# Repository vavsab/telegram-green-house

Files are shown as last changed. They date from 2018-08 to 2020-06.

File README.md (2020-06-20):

# telegram-green-house 
[English version](README.EN.md)

Build Status (https://copter-monitor.visualstudio.com/copter-monitor/_build/latest?definitionId=1&branchName=master)

Открытый телеграм бот, который устанавливается в теплицу. 

## Основные функции:

* Отображение температуры и влажности
* Оповещение при превышениях температуры
* Отображение прогноза из сайта погоды (какого именно, задается в конфигурационном файле)
* Отображение графика температуры за последние сутки
* Запись коротких (до 1 мин) видео и фото из веб-камеры в теплице
* Ручное управление поливом. Управление по отрезкам времени дорабатывается.

# Демо

* [Телеграм-бот](https://t.me/demo_green_house_bot)
* [Эмулятор теплицы](http://demo.green.octopan.net:8081/) - позволяет выставить температуру/влажность и посмотреть, как на нее реагирует бот. Также здесь можно увидеть, включен или выключен свет и полив.
* [Веб-панель](http://demo.green.octopan.net:8080/) - урезанная версия бота. На данный момент только отображает температуру/влажность.

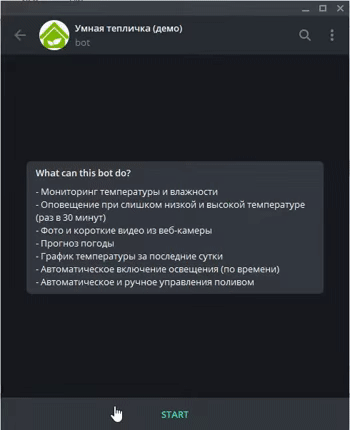
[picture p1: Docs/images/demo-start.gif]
Демо анимация


## Нюансы работы демо

* Отключена проверка прав доступа. В обычной версии нужно добавлять пользователей в конфигурационный файл, чтобы разрешить использование бота.
* Всегда отсылаются примеры фото и видео, т.к. в демо нет настоящей камеры.
* Доступен пример видео только для 5 секунд.

# Применение

Бот предназначен для установки в теплицу, которая находится в непосредственной близости от дома.

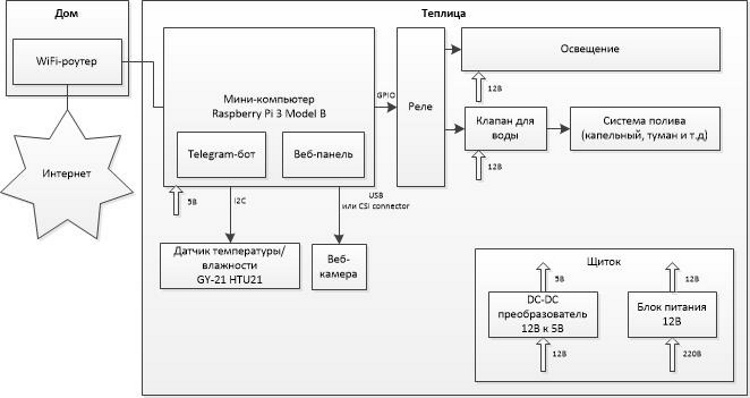
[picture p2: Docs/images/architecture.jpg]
Типичная схема использования


# Цена

Предупреждение:
1. Цены указаны примерно. 
2. Чтобы собрать рабочую модель, нужно обладать базовыми навыками в радиоэлектронике (например, уметь пользоваться паяльником, понимать назначение контактов на датчиках)
3. В инструкциях могут присутствовать недочеты и ошибки. Все делается на свой страх и риск.

Позиция | Цена | Комментарий | Ссылка
--- | --- | --- | ---
Raspberry Pi 3 Model B | $45 | | [Ссылка1](https://arduino.ua/prod1449-raspberry-pi-3-b) [Ссылка2](https://www.olx.ua/list/q-raspberry-pi-3-model-b/)
MicroSD карта Kingston 16GB Class 10 | $8 | Подходит и 8GB. Главное, чтобы Class 10. От флешки зависит стабильность работы Raspberry. Не стоит на этом экономить. | [Ссылка1](https://arduino.ua/prod869-microsd-karta-silicon-power-16gb-class-10--adapter) [Ссылка2](https://elmir.ua/flash_memory_cards/memory_card_micro_sdhc_16gb_kingston_sdc10g2_16gb.html)
Блок питания для Raspberry 5В 3А | $5 | Нужно брать, если пока не планируется управлять поливом или освещением через 12B. Можно использовать имеющийся дома. Но надо смотреть, чтобы он выдавал хотя бы 2A | [Ссылка1](https://arduino.ua/prod2252-blok-pitaniya-impylsnii-5v-3a-microusb)
Комплект перемычек для макетной платы МАМА-МАМА (JUMPERS-FF) - 40шт | $2 | Для соеднения Raspberry с датчиками | [Ссылка1](http://www.kosmodrom.com.ua/el.php?name=JUMPERS-FF-200MM) [Cсылка2](https://www.banggood.com/40pcs-30cm-Female-to-Female-Color-Breadboard-Cable-Jump-Wire-Jumper-p-992836.html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)
Датчик влажности и температуры GY-21 HTU21 | $4 | | [Ссылка1](https://arduino.ua/prod1222-datchik-vlajnosti-i-temperatyri)
Веб-камера | $25-$70 | Опционально. Это может быть как USB, так и оригинальная камера от Raspberry. Перед покупкой USB-камеры проверьте, чтобы камера поддерживалась Raspberry. Например, [здесь](https://elinux.org/RPi_USB_Webcams) | [Raspberry-камера](https://arduino.ua/prod1386-kamera-f-5mp-s-regyliryemim-fokysom-i-nochnim-videniem) [USB-камера](https://rozetka.com.ua/logitech_webcam_c170/p159479/#tab=all)
2-х канальный модуль реле 5В 10А | $2 | Опционально. Для управления поливом и освещением. | [Ссылка1](https://arduino.ua/prod201-2h_kanalnoe_rele_5V_10A)
Магнитный электрический клапан | $7 | Опционально. Для управления поливом. Подбирайте диаметр под свои трубы. Мне подошло 1/2 дюйма. | [Ссылка1](https://arduino.ua/prod369-magnitnii-elektricheskii-klapan-12-duima-zakritii-ot-elecrow)
Блок питания импульсный 12В 200Вт | $11 | Опционально. Для управления освещением, поливом, окнами. Нужно подбирать мощность в зависимости от своих потребностей. | [Ссылка1](https://arduino.ua/prod2408-blok-pitaniya-12v-200vt-16a)
DC-DC понижающий конвертер LM2596 | $2 | Опционально. Для пребразования с 12В на 5В для питания Raspberry | [Ссылка1](https://arduino.ua/prod650-DC-DC-ponijaushhii-konverter-c-4-5-60V-do-3-35V)

# Установка

[Здесь](README.Installation.md) находятся пошаговые инструкции для установки бота на Raspberry.

# План развития

* Добавить управление окнами. Аналогичное [этому](https://www.youtube.com/watch?v=vCNMl9ZpBRg)
* Унифицировать управление освещением, поливом и окнами.
* Сделать уcтановку через npm install.
* Дать возможность администратору разрешать и запрещать доступ другим пользователям.

# Для разработчика

[Здесь](README.Developer.md) находятся инструкции для запуска бота в режиме разработки.

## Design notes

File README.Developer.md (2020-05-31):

# telegram-green-house для разработчика

## Запуск на любой ОС в режиме автоматической перекомпиляции
1. INSTALL nodemon globally: `npm i nodemon -g`
2. Start application: `npm start`

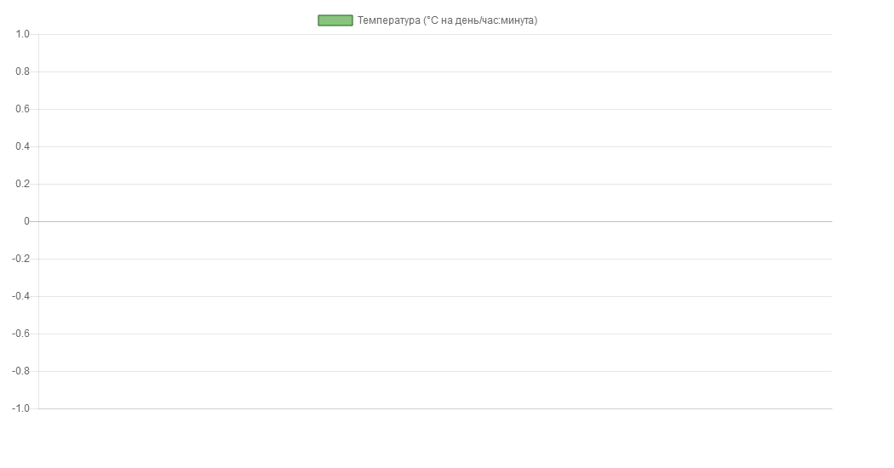
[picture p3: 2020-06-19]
chart.png

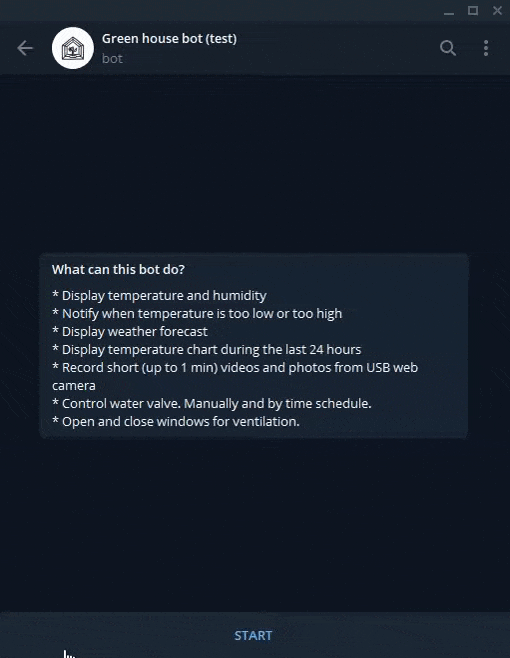
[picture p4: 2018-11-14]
Docs/images/demo-start.en.gif

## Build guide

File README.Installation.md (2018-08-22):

# Установка telegram-green-house

## Схема подключения

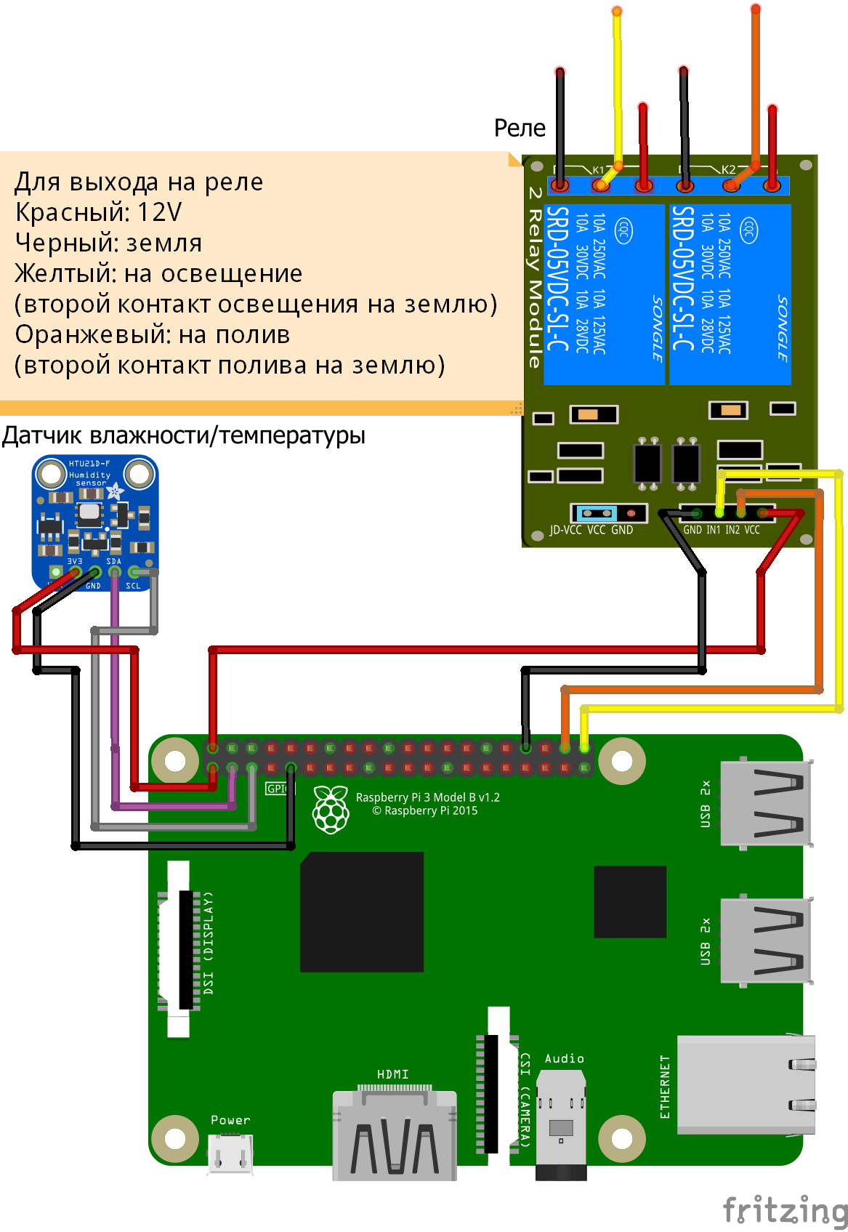
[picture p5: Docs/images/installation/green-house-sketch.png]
Схема подключения


## Установка бота на Raspberry

### Требования
* Базовые навыки работы с коммандной строкой в Linux-системах.
* Наличие персонального компьютера или ноутбука (далее по тексту ПК) с ридером для SD-карт.
* Наличие WiFi-роутера, к которому есть доступ в панель управления.
* Доступ к интернету.

### Шаг 1. Установка операционной системы Raspbian
1. Скачиваем на свой ПК образ операционной системы для Raspberry [RASPBIAN STRETCH LITE](https://www.raspberrypi.org/downloads/raspbian/). Не полную, а именно LITE версию. На момент написания инструкций версия системы была `June 2018`.
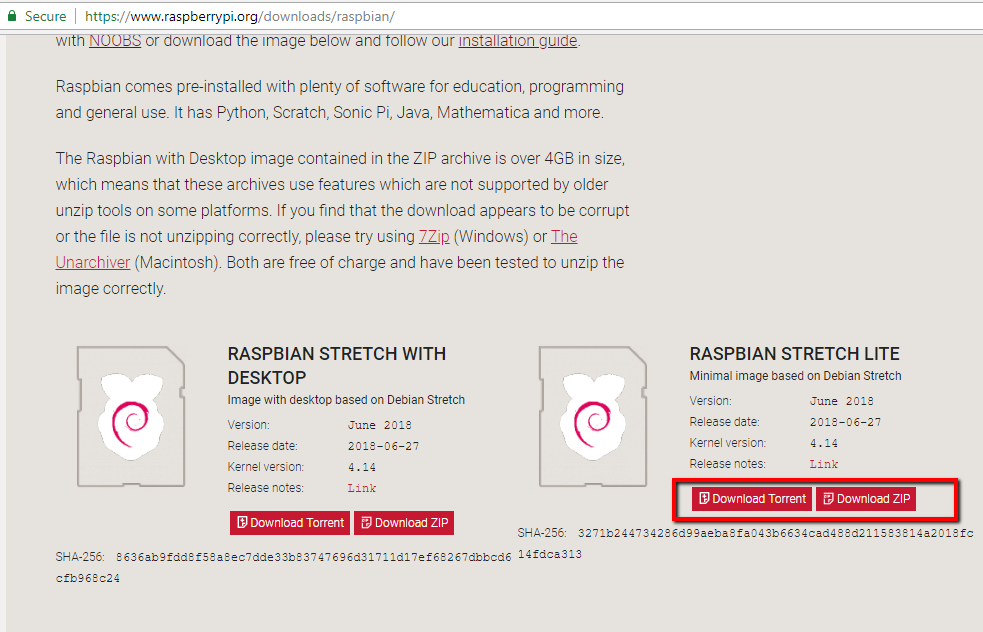
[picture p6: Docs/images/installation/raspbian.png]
Загрузка образа Raspbian
   
2. Записываем образ на micro sd флешку. Это можно сделать при помощи утилиты [Etcher](https://etcher.io/)
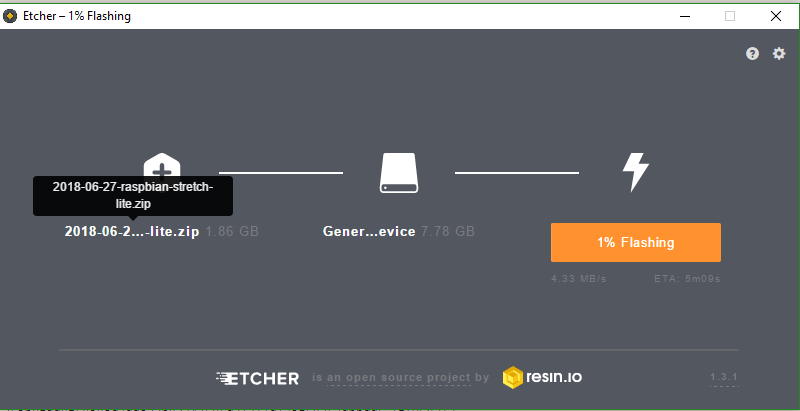
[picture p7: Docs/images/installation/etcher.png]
Запиcь на флеш-накопитель при помощи Etcher
   
   
### Шаг 2. Обеспечение доступа к Raspbian
Нужно беспечить себе доступ к Raspberry. Если есть в наличии USB-клавиатура и HDMI-монитор, то вставляем все вместе с флешкой в Raspberry, подаем на нее питание и работаем, как на обычном компьютере (по умолчанию юзер `pi`, пароль `raspberry`). У меня же была только Raspberry и домашний WiFi-роутер. С этом случае нужно:

1. Отредактировать на флешке файл `/etc/wpa_supplicant/wpa_supplicant.conf`, чтобы Rasbperry автоматически при старте подключилась к Wi-Fi. Если у Вас ПК на Windows, то просто так не получится отредактировать флешку (только boot раздел), потому что там другая фаловая система и Windows ее не видит. Исправить это поможет утилита [Ext2FSD](http://www.ext2fsd.com/?page_id=16). После установки Windows увидит флешку. Открываем `/etc/wpa_supplicant/wpa_supplicant.conf`, пишем туда и сохраняем:<br />
    ```
    ctrl_interface=/run/wpa_supplicant
    update_config=1
    network={
        ssid="МояДомашняяСеть"
        psk="СуперПарольОтСети"
    }
    ```
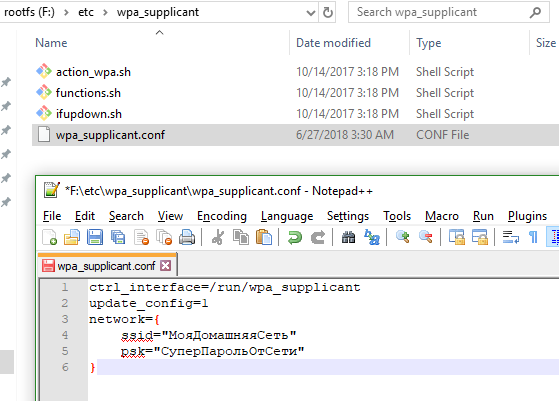
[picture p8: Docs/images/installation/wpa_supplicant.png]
Редактирование подключения к Wi-Fi
    
2. Нужно настроить ssh для удаленного доступа к Raspberry. Есть в Raspbian простой способ. В boot разделе (который намного меньше по размеру и виден для Windows сразу, без установки Ext2FSD) создаем пустой файл `ssh` без расширений типа  ~~`ssh.txt`~~. Если Raspbian при загрузке видит этот файл, то активирует ssh. [Источник](https://www.raspberrypi.org/forums/viewtopic.php?t=169905)
3. Безопасно извлекаем флешку. Правой кнопкой мыши по boot и rootfs разделам и выбираем "Извлечь". Если вытащить без безопасного извлечения, то есть вероятность потерять изменения.
4. Вставляем флешку в Raspberry и запускаем ее.
5. Теперь на ПК нужно установить клиент для ssh. Например, [MobaXterm](https://mobaxterm.mobatek.net/download.html). Бесплатной версии вполне хватит.
6. Если все прошло успешно, то в панели администрирования в WiFi-роутере должна появиться `raspberrypi`. Нужно узнать, какой у нее IP-адрес. Обычно в роутерах эта информация находится во вкладке DHCP.
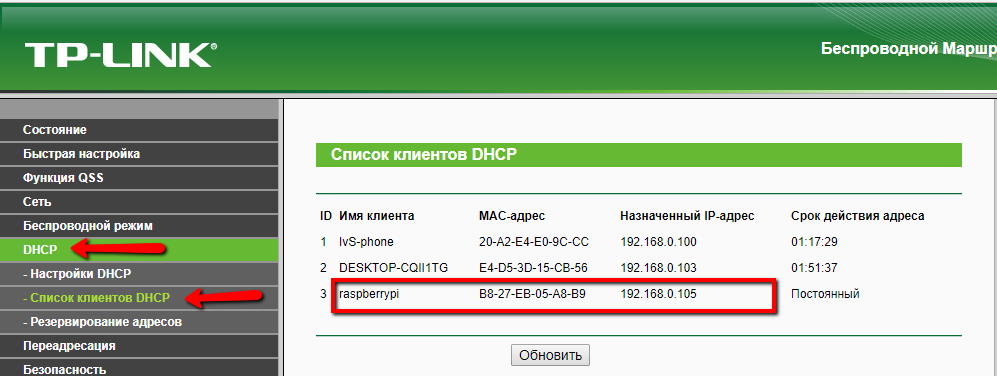
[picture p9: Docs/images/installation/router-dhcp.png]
Пример отображения IP адреса на роутере
   
7. Создаем SSH-сессию в MobaXterm. Если все правильно сконфигурировано, то консоль предложит ввести логин/пароль. По умолчанию юзер `pi`, пароль `raspberry`.
   
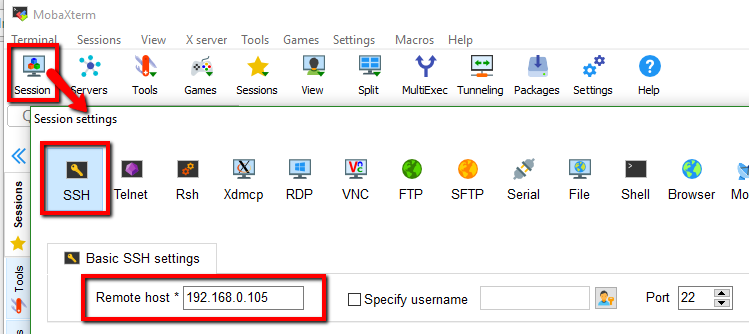
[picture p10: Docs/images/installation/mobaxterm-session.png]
Конфигурация MobaXterm
    
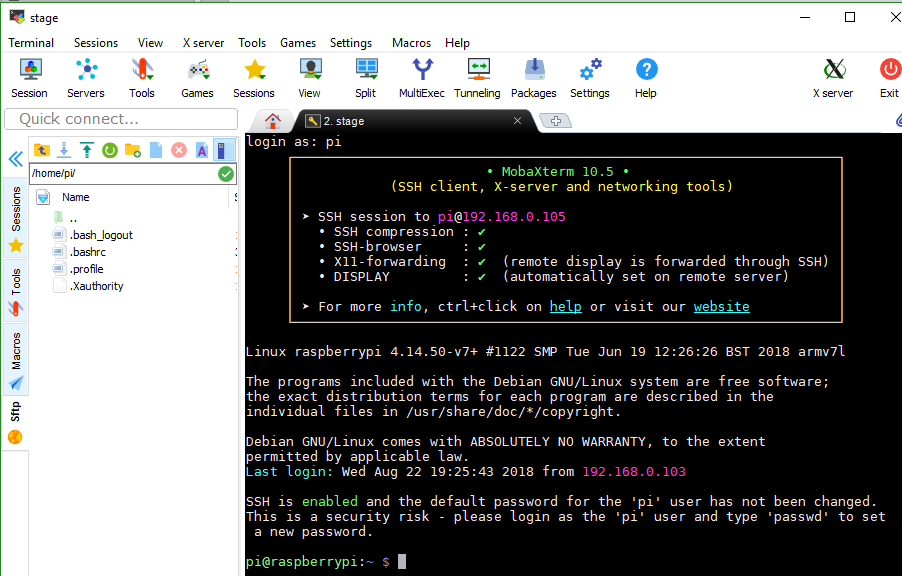
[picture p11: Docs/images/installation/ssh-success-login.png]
Успешный вход по SSH
    
8. После входа **обязательно** меняем стандартный пароль командой `sudo passwd pi`. Иначе Вас легко взломают. Если сложно придумать хороший пароль, то его всегда можно [сгенерировать](https://passwordsgenerator.net/ru/)

### Шаг 3. Установка библиотек для работы бота
1. Переходим в домашний каталог и там создаем директорию для будущего бота
    ```
        cd /home/pi/
        mkdir green-house
        cd green-house
    ```
2. В директории для бота создаем временную папку для установки библиотек и переходим в пользователя root
    ```
        mkdir install
        cd install
        sudo su
    ```
3. Устанавливаем NodeJS (среда для выполнения кода JavaScript). Устанавливаем именно **8.х**, не 10.х. Новая версия NodeJS пока что несовместима с библиотеками для работы с I2C (датчик влажности/температуры).
    ```
    curl -sL https://deb.nodesource.com/setup_8.x | sudo -E bash -
    apt-get install -y nodejs
    ```
4.  Устанавливаем PM2 (менеджер процессов)
    ```
    npm i pm2 -g
    ```
5.  Устанавливаем BCM2835 (библиотека для работы с пинами GPIO)
    ```
    wget http://www.airspayce.com/mikem/bcm2835/bcm2835-1.50.tar.gz
    tar xvfz bcm2835-1.50.tar.gz
    cd bcm2835-1.50;
    ./configure
    make
    make install
    cd ..
    ```
    [Источник](https://gist.github.com/annem/3183536)
6. Активируем интерфейс I2C (для коммуникации с датчиком температуры/влажности)
    ```
    raspi-config
    ```
   В меню переходим: `Interfacing options => I2C => Yes => Finish`<br />
   [Источник](https://learn.adafruit.com/adafruits-raspberry-pi-lesson-4-gpio-setup/configuring-i2c)
7.  Устанавливаем PhantomJS (библиотека для рендеринга веб-страниц. Нужна для графиков температуры и прогноза погоды)
    ```
    wget https://github.com/fg2it/phantomjs-on-raspberry/releases/download/v2.1.1-wheezy-jessie-armv6/phantomjs_2.1.1_armhf.deb
    dpkg -i phantomjs_2.1.1_armhf.deb
    # С первого раза PhantomJS не установится
    apt --fix-broken install
    dpkg -i phantomjs_2.1.1_armhf.deb
    ```
    [Источник](https://github.com/fg2it/phantomjs-on-raspberry)
8.  Устанавливаем MongoDB (база данных для сохранения показаний датчиков)
    ```
    apt-get install -y mongodb
    ```
9. Устанавливаем git (для скачивания файлов бота из репозитория)
    ```
    apt-get install -y git
    ```
11. Устанавливаем fswebcam (для захвата изображений из камеры)
    ```
    apt-get install -y fswebcam
    ```
    *Заметка*: Если Вы используете оригинальную камеру, которая крепится при помощи шлейфа к raspberry (не USB), то ее нужно дополнительно активировать через команду `raspi-config`. В меню переходим: `Interfacing options => Camera => Yes => Finish`
12. Удаляем временную папку `install`
    ```
    cd /home/pi/green-house
    rm -R install
    ```
13. Перезагружаем Raspberry 
    ```
    reboot
    ```

### Шаг 4. Установка бота
1. Переходим в каталог для бота
   ```
   cd /home/pi/green-house
   ```
2. Скачиваем сборку бота из репозитория
    ```
    git clone --depth=1 https://github.com/vavsab/telegram-green-house-build .
    ```
3. Устанавливаем NodeJS зависимости для бота 
    ```
    sudo npm install --unsafe-perm
    ```
4. Получаем токен от [@BotFather](https://t.me/BotFather).<br />
   [Источник](http://fstrk.io/blog/telegram_newbot)
5. Создаем `config.js` и заменяем в нем токен на свой. Токен находится в настройке `bot.token`
    ```
    cp config.default.json config.json
    nano config.json
    ```
    *Заметка*: чтобы выйти и сохранить в редакторе nano, нужно нажать Ctrl+X, а потом Y.
6. Запускаем бота и ставим его на автозапуск при старте Raspberry
   ```
   sudo pm2 start ecosystem.config.js
   sudo pm2 save
   sudo pm2 startup
   ```
7. Проверяем по логам, что бот действительно запустился
    ```
    sudo pm2 logs
    ```
8. Находим своего бота в Telegram, и проверяем, что он отвечает на сообщения.
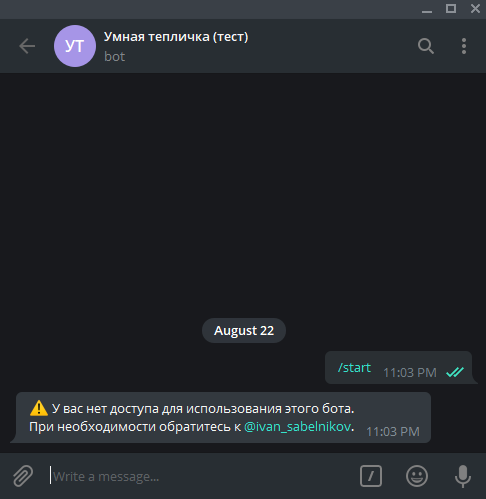
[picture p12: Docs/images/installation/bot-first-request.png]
Первое обращение к боту
   
9.  Для того, чтобы открыть доступ, нужно знать идентификатор пользователя. Первое обращение пользователя бот пишет в логи:
    ```
    sudo pm2 logs
    ```
    Логи при первом обращении пользователя
10. Открываем `config.js` и назначаем себя админом, заменив идентификатор в настройке `bot.adminChatId`, а также добавляем себя к пользователям бота в настройке `bot.allowedChatIds`. Администратор может быть только один. А пользователей может быть много. Добавлять их нужно по тому же принципу.
    
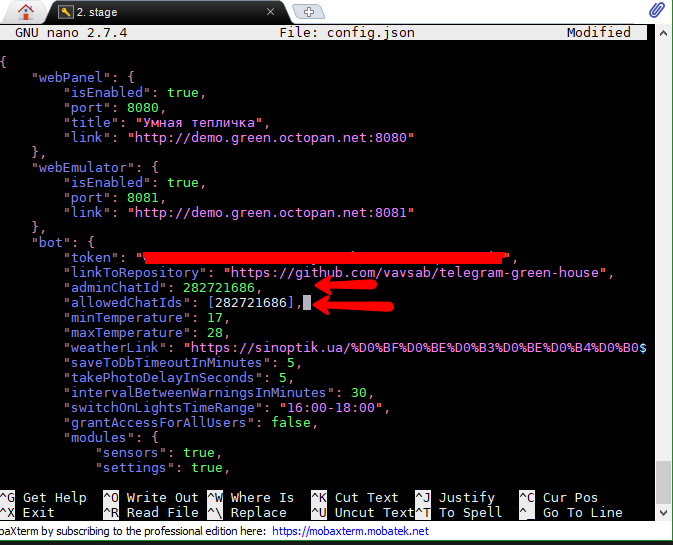
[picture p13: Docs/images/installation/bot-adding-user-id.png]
Добавление администратора
    
11. Перезапускаем бота, чтобы применить настройки:
    ```
    sudo pm2 restart all
    ```
12. После перезапуска напишите боту - он должен отобразить свою клавиатуру:
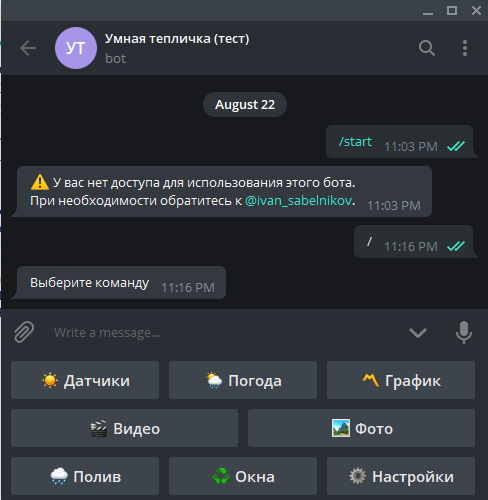
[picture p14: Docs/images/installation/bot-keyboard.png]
Реакция бота на авторизированного пользователя


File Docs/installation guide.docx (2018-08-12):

Установка:
1. Образ
2. Etcher
3. Ext2FSD: http://www.ext2fsd.com/?page_id=16
4. Изменить файлы для работы с Wi-Fi
http://weworkweplay.com/play/automatically-connect-a-raspberry-pi-to-a-wifi-network/
5. Изменить файлы для активации SSH
https://www.raspberrypi.org/forums/viewtopic.php?t=169905
6. MobaXTerm https://mobaxterm.mobatek.net/download-home-edition.html
7. Change hostname: https://thepihut.com/blogs/raspberry-pi-tutorials/19668676-renaming-your-raspberry-pi-the-hostname or sudo raspi-config
8. Change ssh password: https://raspberrypi.stackexchange.com/questions/4409/how-do-i-change-recover-my-password sudo passwd pi

8.1 install git (для лайт версии разбери)

sudo apt-get install git

9. git clone --depth=1 <url> .

10. curl -sL https://deb.nodesource.com/setup_8.x | sudo -E bash -

sudo apt-get install -y nodejs

11. sudo su

npm i pm2 -g

12. BCM: https://gist.github.com/annem/3183536

enable I2c https://learn.adafruit.com/adafruits-raspberry-pi-lesson-4-gpio-setup/configuring-i2c

(repeat on every install)

npm install i2c rpio raspi raspi-serial --unsafe-perm --save

12.5 https://github.com/fg2it/phantomjs-on-raspberry

wget https://github.com/fg2it/phantomjs-on-raspberry/releases/download/v2.1.1-wheezy-jessie-armv6/phantomjs_2.1.1_armhf.deb

dpkg -i phantomjs_2.1.1_armhf.deb

apt --fix-broken install (for lite raspian)

dpkg -i phantomjs_2.1.1_armhf.deb

13. npm i --production

13.5 apt-get install mongodb

Create bot and get token. Setup config

cp ecosystem.config.default.js ecosystem.config.js

14. pm2 start ecosystem.config.js

pm2 save

pm2 startup

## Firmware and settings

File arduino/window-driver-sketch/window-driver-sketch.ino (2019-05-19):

// Import library from https://github.com/rkoptev/ACS712-arduino
#include <ACS712.h>

enum State {
  StateStart,
  StateClosed,
  StateClosing,
  StateOpen,
  StateOpening,
  StateError
} state;

#define CommandReset   "reset"
#define CommandClose   "close"
#define CommandOpen    "open"
#define CommandState   "state"

#define UARTPin           8
#define RS485Transmit     HIGH
#define RS485Receive      LOW 
#define MessageDelimiter  "#"
#define MessageBufferSize 8     // 1 for address + 1 delimiter + 5 for command + "\0". Example "5#state"

#define LimitSwitchUpPin            2
#define LimitSwitchDownPin          3
#define LimitSwitchEnabled          LOW
#define LimitSwitchDisabled         HIGH
#define LimitSwitchReleaseTimeout   1000 // Time in ms that is needed to release opposite limit switch. Fof example, to release down switch when opening a window
#define LimitSwitchOpenCloseTimeout 9000 // Time in ms that is needed to open/close a window
#define LimitSwitchBounceTimeout 5000 // Time in ms for allowing contact bouncing 

#define RelayUpPin      7
#define RelayDownPin    6
#define RelayEnable     LOW
#define RelayDisable    HIGH

#define ErrorLEDPin       13
#define ErrorLEDEnable    HIGH
#define ErrorLEDDisable   LOW

#define MaxAllowedCurrent 5 // Amperes
#define VoltageSurgeTimeout 100 // Time in ms for allowing big current (engine requires a big current to start)

byte limitSwitchUp = LimitSwitchDisabled;
byte limitSwitchDown = LimitSwitchDisabled;
byte relayUp = RelayDisable;
byte relayDown = RelayDisable;
byte errorLED = ErrorLEDDisable;

String lastError = "";
String lastCommand = "";
char messageBuffer[MessageBufferSize];
int messageBufferIndex = 0;
int messageAddress = 3;
float current = 0;
ACS712 currentSensor(ACS712_30A, A0);
unsigned long lastStateChangeTime;

void setup() {
  pinMode(RelayDownPin, OUTPUT);
  pinMode(RelayUpPin, OUTPUT);
        
  pinMode(ErrorLEDPin, OUTPUT);
  pinMode(UARTPin, OUTPUT);
  
  pinMode(LimitSwitchUpPin, INPUT_PULLUP);
  pinMode(LimitSwitchDownPin, INPUT_PULLUP);

  setOutPins();
  lastStateChangeTime = millis();

  Serial.begin(9600);
  Serial.println("Started");
}

void loop() {
  limitSwitchUp = digitalRead(LimitSwitchUpPin);
  limitSwitchDown = digitalRead(LimitSwitchDownPin);
  current = -currentSensor.getCurrentDC(); // TODO: Fix minus current

  updateLastCommand();
  responseToMessage();
  updateState();
  lastCommand = "";
  setOutPins();
}

void updateLastCommand() {
  while (Serial.available() > 0) {
      char incomingChar;
      incomingChar = char(Serial.read());
      
      if (incomingChar == '\n') {
        messageBuffer[messageBufferIndex] = '\0';
        messageBufferIndex = 0;
        char* token = strtok(messageBuffer, MessageDelimiter);
        if (token == NULL)
          return;

        int address = atoi(token);
        if (address != messageAddress)
          return;
        
        token = strtok(NULL, MessageDelimiter);
        if (token == NULL)
          return;

        lastCommand = token;
        Serial.println("Parsed command: " + lastCommand);
      } else {
        messageBuffer[messageBufferIndex] = incomingChar;
        messageBufferIndex++;
      }

      if (messageBufferIndex >= MessageBufferSize) {
          messageBufferIndex = 0;
          Serial.println("Error while parsing command: " + String(messageBuffer));
      }
  }
}

void responseToMessage() {
  if (lastCommand != CommandState) 
    return;

  Serial.flush(); // Finish sending debug data
  digitalWrite(UARTPin, RS485Transmit);
  delay(1); // It takes some time to set the pin
  Serial.println(getCurrentState());
  Serial.flush(); // Finish sending RS485 data
  digitalWrite(UARTPin, RS485Receive);
  delay(1); // It takes some time to set the pin
}

void updateState() {
  State oldState = state;
  unsigned long msOnCurrentState = millis() - lastStateChangeTime;

  if (state != StateError && current > MaxAllowedCurrent && msOnCurrentState > VoltageSurgeTimeout) {
    setError("HIGH_CURRENT"); // Too high current on state X
  } else if (lastCommand == CommandReset) {
    state = StateStart;
  } else {
    switch (state) {
      case StateStart:
        errorLED = ErrorLEDDisable;
        relayUp = RelayDisable;
        relayDown = RelayDisable;
        
        if (limitSwitchUp == LimitSwitchEnabled && limitSwitchDown == LimitSwitchEnabled) {
          setError("UP_DOWN_ENABLED"); // Start failure. Up and down limits have been enabled.
        } else if (limitSwitchUp == LimitSwitchEnabled && limitSwitchDown == LimitSwitchDisabled) {
          state = StateOpen;
        } else if (limitSwitchUp == LimitSwitchDisabled && limitSwitchDown == LimitSwitchEnabled) {
          state = StateClosed;
        } else if (limitSwitchUp == LimitSwitchDisabled && limitSwitchDown == LimitSwitchDisabled) {
          state = StateClosing;
        }
        
        break;
        
      case StateClosed:
        errorLED = ErrorLEDDisable;
        relayUp = RelayDisable;
        relayDown = RelayDisable;
        
        if (limitSwitchUp == LimitSwitchEnabled) {
          setError("UP_ENABLED"); // Closed failure. Up limit has been enabled.
        } else if (limitSwitchDown == LimitSwitchDisabled && msOnCurrentState > LimitSwitchBounceTimeout) {
          setError("DOWN_DISABLED"); // Closed failure. Down limit has been disabled.
        } else if (lastCommand == CommandOpen) {
          state = StateOpening;
        }
        
        break;
        
      case StateClosing:
        errorLED = ErrorLEDDisable;
        relayUp = RelayDisable;
        relayDown = RelayEnable;

        if (limitSwitchUp == LimitSwitchEnabled && msOnCurrentState > LimitSwitchReleaseTimeout) {
          setError("TIMEOUT_UP_STILL_ENABLED"); // Closing timeout. Up limit is still enabled
        } else if (limitSwitchDown == LimitSwitchDisabled && msOnCurrentState > LimitSwitchOpenCloseTimeout) {
          setError("TIMEOUT_DOWN_NOT_ENABLED"); // Closing timeout. Down limit has not been enabled
        } else if (limitSwitchDown == LimitSwitchEnabled) {
          state = StateClosed;
        } else if (lastCommand == CommandOpen) {
          state = StateOpening;
        }
        
        break;
        
      case StateOpen:
        errorLED = ErrorLEDDisable;
        relayUp = RelayDisable;
        relayDown = RelayDisable;
        
        if (limitSwitchDown == LimitSwitchEnabled) {
          setError("DOWN_ENABLED"); // Open failure. Down limit has been enabled
        } else if (limitSwitchUp == LimitSwitchDisabled && msOnCurrentState > LimitSwitchBounceTimeout) {
          setError("UP_DISABLED"); // Open failure. Up limit has been disabled.
        } else if (lastCommand == CommandClose) {
          state = StateClosing;
        }
        
        break;
        
      case StateOpening:
        errorLED = ErrorLEDDisable;
        relayUp = RelayEnable;
        relayDown = RelayDisable;

        if (limitSwitchDown == LimitSwitchEnabled && msOnCurrentState > LimitSwitchReleaseTimeout) {
          setError("TIMEOUT_DOWN_STILL_ENABLED"); // Opening timeout. Down limit is still enabled
        } else if (limitSwitchUp == LimitSwitchDisabled && msOnCurrentState > LimitSwitchOpenCloseTimeout) {
          setError("TIMEOUT_UP_NOT_ENABLED"); // Opening timeout. Up limit has not been enabled
        } else if (limitSwitchUp == LimitSwitchEnabled) {
          state = StateOpen;
        } else if (lastCommand == CommandClose) {
          state = StateClosing;
        }
        
        break;
        
      case StateError:
        errorLED = ErrorLEDEnable;
        relayUp = RelayDisable;
        relayDown = RelayDisable;

        break;
    }
  }

  if (oldState != state) {
    lastStateChangeTime = millis();
    Serial.println("State has been changed to " + getCurrentState());
  }
}

void setOutPins() {
  digitalWrite(RelayUpPin, relayUp);
  digitalWrite(RelayDownPin, relayDown);
  digitalWrite(ErrorLEDPin, errorLED);

  // To debug without RS485 set to transmit
  digitalWrite(UARTPin, RS485Receive);
}

void setError(String errorDescr) {
  lastError = getCurrentState() + "#" + errorDescr;
  state = StateError;
}

String getCurrentState() {
  switch (state) {
    case StateStart:
      return "start";
    case StateClosed:
      return "closed";
    case StateClosing:
      return "closing";
    case StateOpen:
      return "open";
    case StateOpening:
      return "opening";
    case StateError:
      return "error#" + lastError;
    default:
      return "";
  }
}

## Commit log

2018-08-22 Add connection scheme
    [green-house-sketch.fzz]
2018-08-22 Change raspberry price
2018-08-22 Add RPi Camera activation
2018-08-23 Modified installation sketch
    [green-house-sketch.fzz]
2018-08-23 Fix water pin number to match installation guide
2018-08-31 Windows > 1) Adjust driver timeouts 2) Fix driver current control 3) Fix RS485 to work in duplex mode
    [window-driver-sketch.ino]
2018-08-31 Windows > Raspberry > Fix RS485 to work in duplex mode
2018-09-11 Arduino sketch - 1) Fix max current state overflow 2) Fix RS485 initial state
    [window-driver-sketch.ino]
2018-09-30 Improve windows control with additional buttons
2018-11-14 Fix case of links
2019-05-19 1) Increase windows open and close timeouts from 7 sec to 9 sec 2) Make short error codes to fix collisions when fetching data from all windows 3) Localize windows error messages
    [window-driver-sketch.ino]
2019-06-08 Add ability to have several watering valves
2020-06-19 Edit sensors threshold
2020-06-21 Move sensors & photo config info db
